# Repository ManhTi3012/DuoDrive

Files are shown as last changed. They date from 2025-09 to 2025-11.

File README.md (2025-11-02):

# ⚠️ **WARNING: PROJECT UNDER DEVELOPMENT, CHANGES WILL BE MADE**
<p align="center" style="display: flex; gap: 10px;">
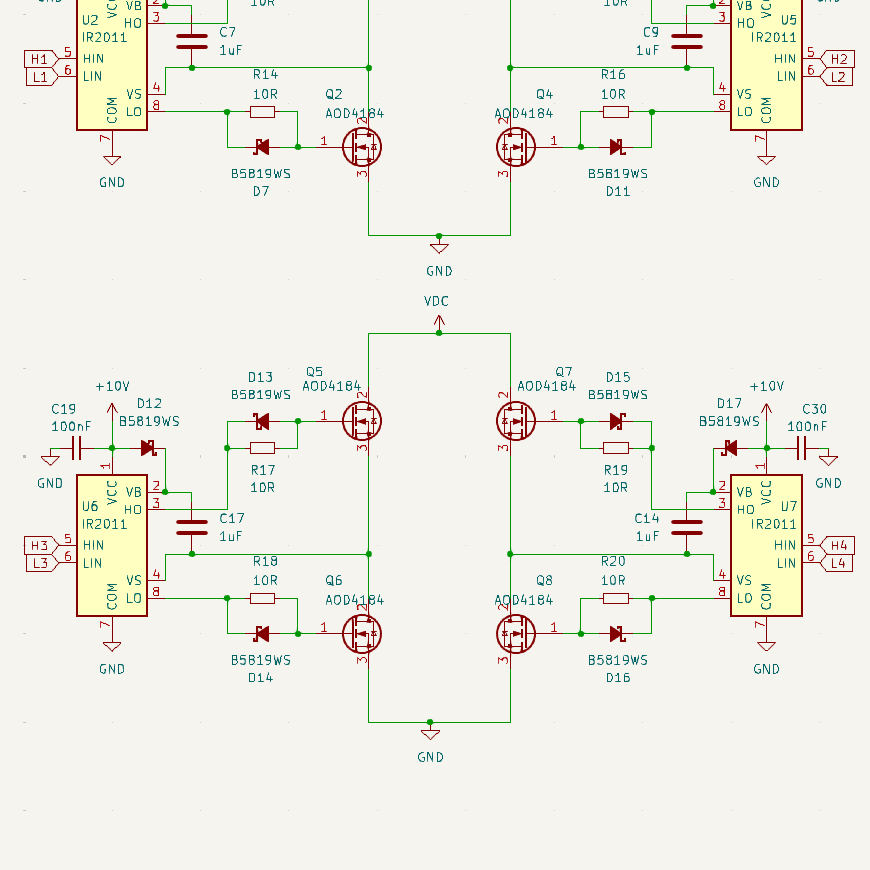
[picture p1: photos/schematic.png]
  
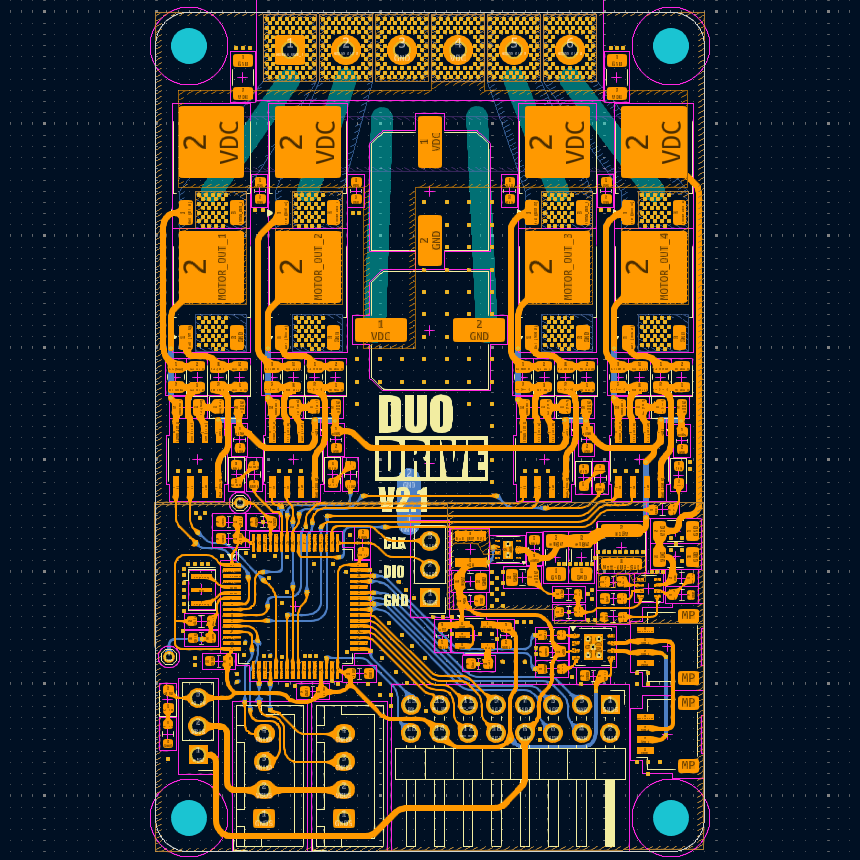
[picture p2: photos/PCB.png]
  
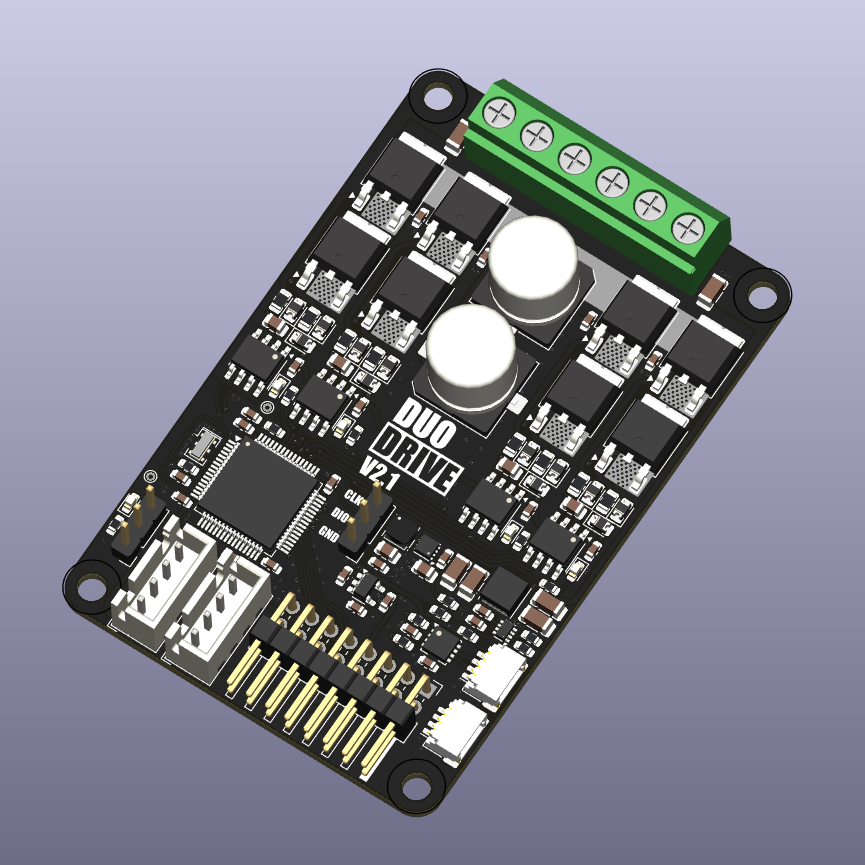
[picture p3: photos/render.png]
  
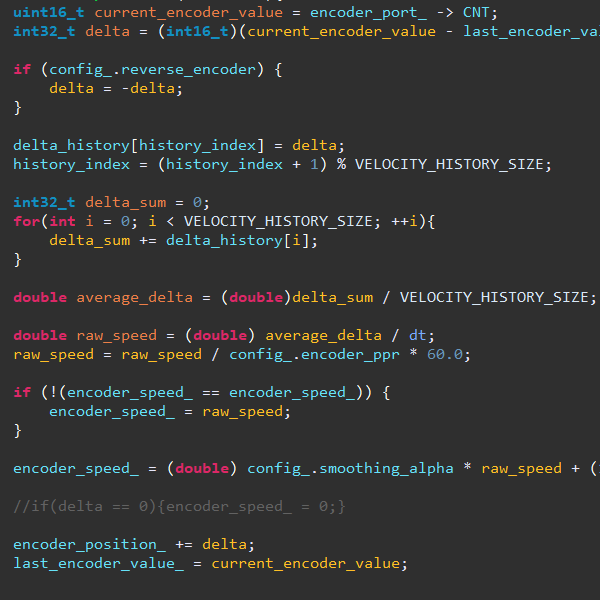
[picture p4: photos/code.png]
  
</p>

# DuoDrive
DuoDrive is a closed-loop brushed motor driver design to offer simple and affordable open-source hardware and software:
* Running internal PID loop for driving up to 2 brushed motor.
* Increment-type and absolute-type encoder (not yet).
* UART interface and CAN Bus (no firmware support yet).
* Velocity and position control.

You can also use SimpleFOC library to control a single BLDC motor.

<!---  An autonomous robot using DuoDrive's velocity control can still run straight without line or gyro correction.
  ![hi](https://github.com/ManhTi3012/DuoDrive/blob/main/photos/robot.gif) --->

For configuring the driver, checkout the [Web Tool](https://manhti3012.github.io/DuoDriveConfigTool/)

# Hardware
DuoDrive is designed to handle high current within a small footprint:
* Voltage input: 12-24v, 30V absolute maximum
* Maximum continuous current: 25A
* Power traces are exposed for high current handling, beware of shorts
* Dimensions: 49mm x 75mm

Step file can be found in "3D" folder.
# Firmware
The firmware is expected to be stable for now, but further testing still needed for stability-related bugs.
Please open a new issues if you encounter any problem.
For detailed explanation and methods, check Wiki page.

# Documentation
For more detail, check the [WIKI Page](https://github.com/ManhTi3012/DuoDrive/wiki)

# Liability
* The software and hardware are still in development and may contain bugs, errors, or incomplete features.
* Users are encouraged to use this software and hardware responsibly and at their own risk.

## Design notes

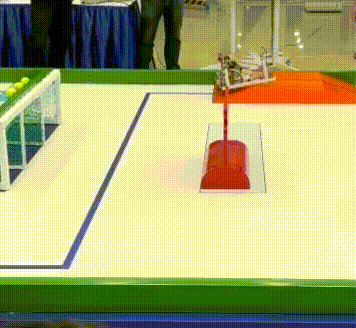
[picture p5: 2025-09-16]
photos/robot.gif

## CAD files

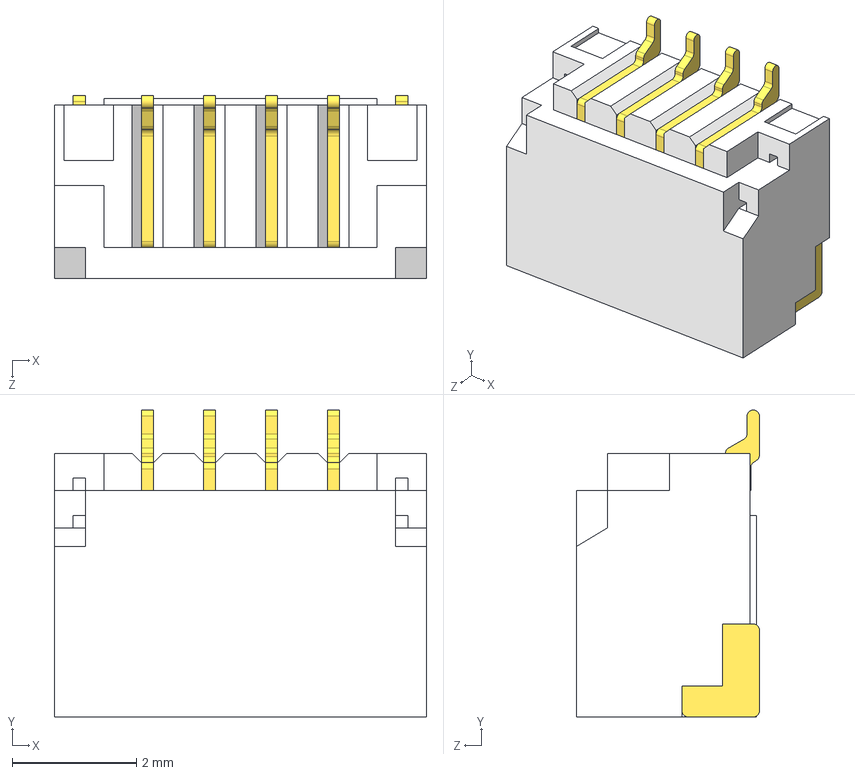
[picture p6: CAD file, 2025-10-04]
3D/SH1.0 Straight 4P.STEP
6.00 x 4.95 x 2.95 mm

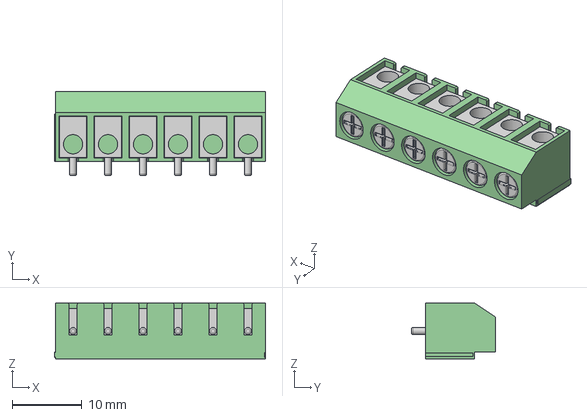
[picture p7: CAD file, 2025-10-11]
3D/Screw Terminal Block 5mm 6-way.step
30.1 x 12.0 x 8.00 mm

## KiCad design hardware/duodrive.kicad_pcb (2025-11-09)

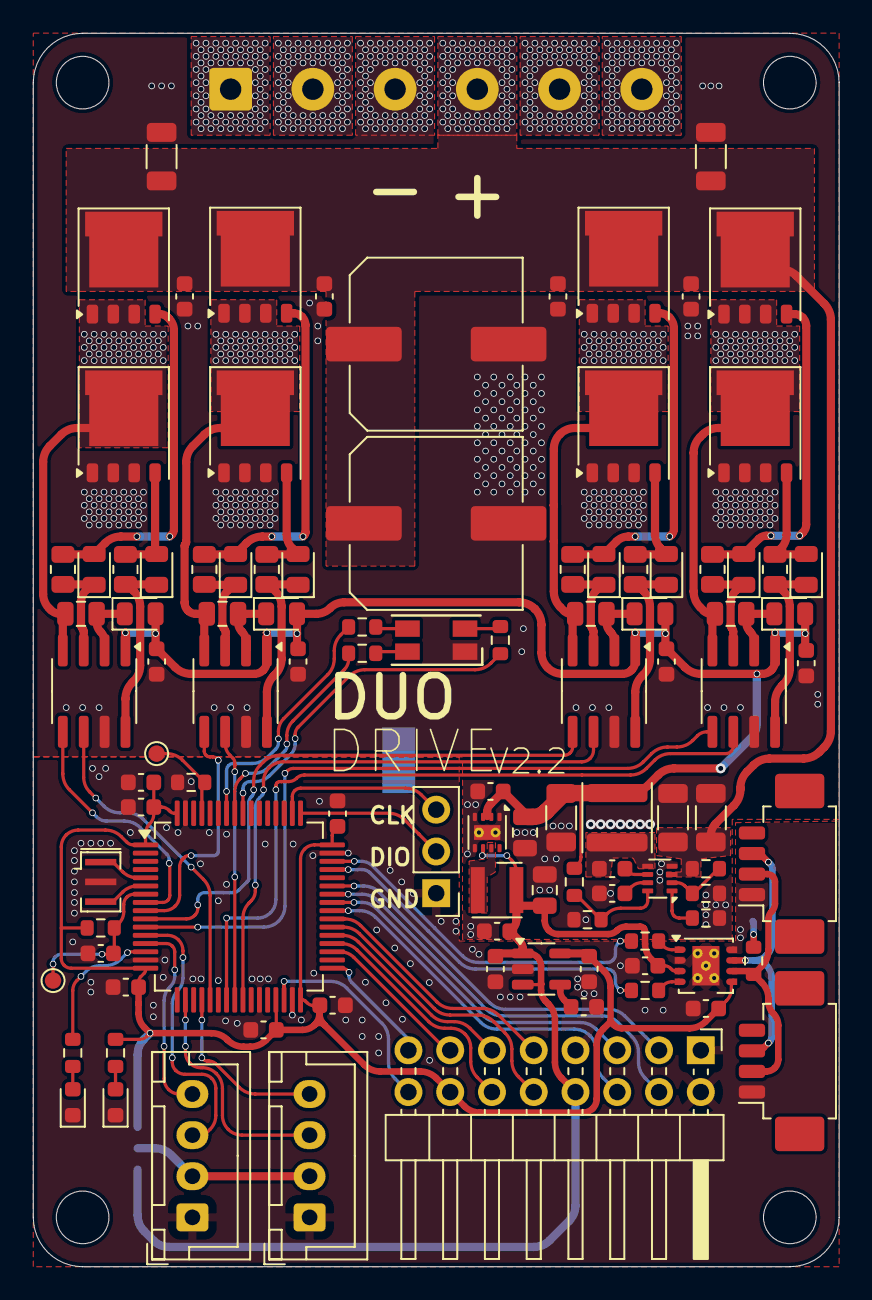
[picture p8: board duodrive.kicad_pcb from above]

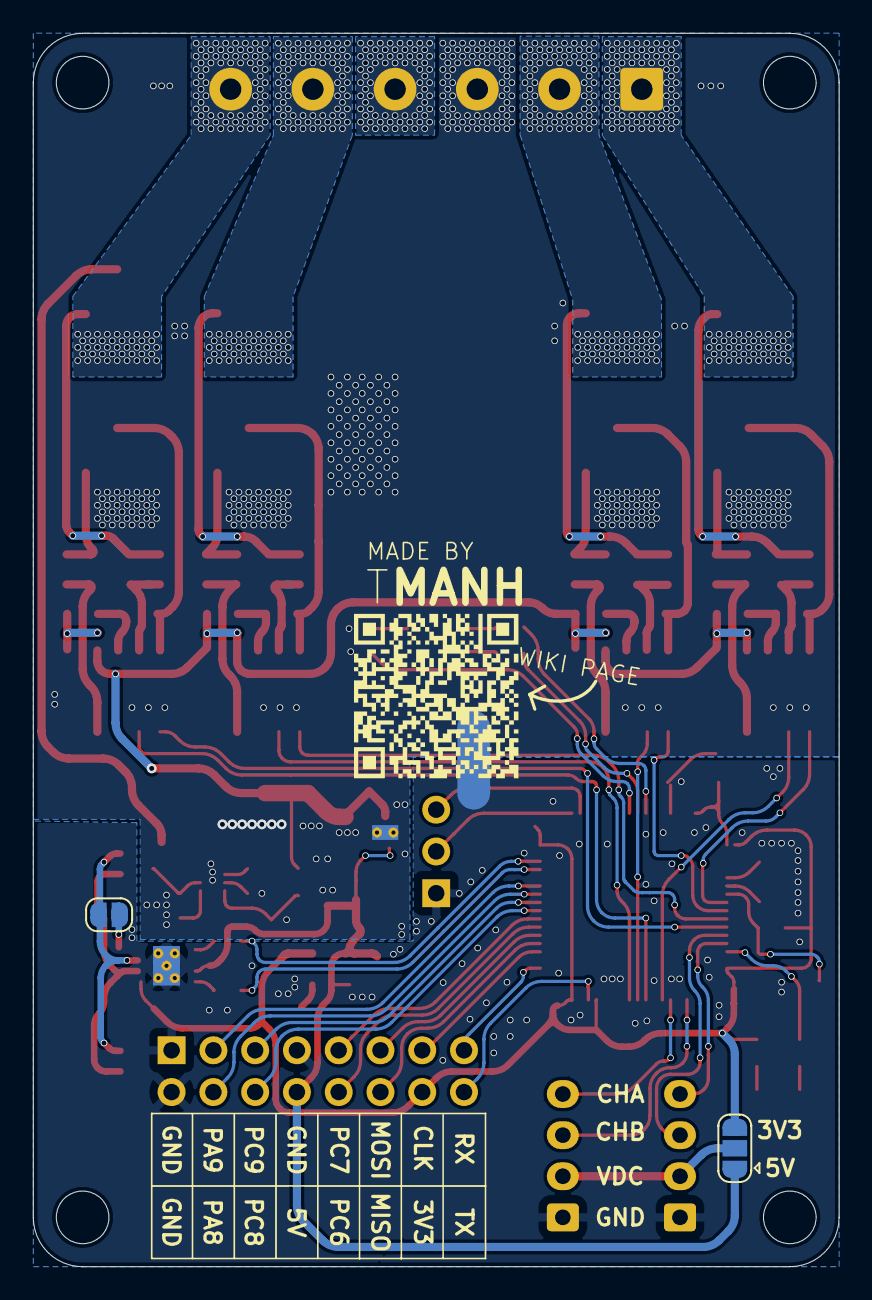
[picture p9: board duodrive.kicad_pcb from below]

Board: 2 copper layers, 49.0 x 75.0 mm, 111 parts (3 on the bottom side), 84 nets.

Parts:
C1, C3: 470uF; C_Elec_10x10.2
C2, C4, C5, C6, C8, C11, C13, C15, C16, C19, C21, C22, C25, C30, C36, C41, C42: 100nF; C_0603_1608Metric
C7, C9, C14, C17: 1uF; C_0805_2012Metric
C10, C12: 10uF; C_0603_1608Metric
C18, C20, C27: 10uF; C_1206_3216Metric
C23, C24: 22uF; C_1206_3216Metric
C26: 470pF; C_0603_1608Metric
C29, C31: 22uF; C_0805_2012Metric
C32, C33, C34, C35: 1uF; C_0603_1608Metric
D1, D20: LED_Small; LED_0603_1608Metric
D4: LED_KRGB; LED_RGB_1210
D6, D7, D8, D9, D10, D11, D12, D13, D14, D15, D16, D17: B5819WS; D_0805_2012Metric
H1, H2, H3, H4: MountingHole_Pad; MountingHole_3.2mm_M3
J2: Conn_02x08_Odd_Even; PinHeader_2x08_P2.54mm_Horizontal
J3: SWD; PinHeader_1x03_P2.54mm_Vertical
J4: CAN_IN; Molex_PicoBlade_53261-0471_1x04-1MP_P1.25mm_Horizontal
J5: CAN_OUT; Molex_PicoBlade_53261-0471_1x04-1MP_P1.25mm_Horizontal
J6: POWER; TerminalBlock_MetzConnect_Type094_RT03506HBLU_1x06_P5.00mm_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
J7: ENCODER1; JST_XH_B4B-XH-A_1x04_P2.50mm_Vertical
J8: ENCODER2; JST_XH_B4B-XH-A_1x04_P2.50mm_Vertical
JP1: Jumper_2_Open; SolderJumper-2_P1.3mm_Open_RoundedPad1.0x1.5mm
JP2: Jumper_3_Open; SolderJumper-3_P1.3mm_Open_RoundedPad1.0x1.5mm
L1: 12uH; L_APV_ANR4020
L2: 2.2uH; L_Wurth_WE-LQSH-3012
NT1: NetTie_2; NetTie-2_SMD_Pad2.0mm
Q1, Q2, Q3, Q4, Q5, Q7: DON50N04; PQFN-8-EP_6x5mm_P1.27mm_Generic
Q6, Q8: NMOS-8PINS; PQFN-8-EP_6x5mm_P1.27mm_Generic
R1, R3, R8, R9, R10, R11: 1K; R_0603_1608Metric
R2, R5, R6: 10K; R_0603_1608Metric
R4: 115K; R_0603_1608Metric
R7: 470K; R_0603_1608Metric
R12: 56K; R_0603_1608Metric
R13, R14, R15, R16, R17, R18, R19, R20: 10R; R_0805_2012Metric
R21, R22: 47R; R_0603_1608Metric
R23: 120R; R_0603_1608Metric
TP1, TP2: TestPoint; TestPoint_Pad_D1.0mm
U1: TCAN1044V; Texas_S-PVSON-N8_ThermalVias
U2, U5, U6, U7: UCC27211; SOIC-8_3.9x4.9mm_P1.27mm
U3: TPS62173DSG; WSON-8-1EP_2x2mm_P0.5mm_EP0.9x1.6mm_ThermalVias
U4: STM32G431RBTx; LQFP-64_10x10mm_P0.5mm
U8: TPS62933; SOT-583-8
U10: MIC5219-3.3YM5; SOT-23-5
Y1: Resonator; Resonator_SMD_Murata_CSTxExxV-3Pin_3.0x1.1mm

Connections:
+3.3V: C2.1, C4.1, C8.1, C11.1, C12.1, C21.1, C22.1, C36.1, J2.14, JP2.3 (B), R5.2, R8.1, U1.5 (VIO), U4.1 (VBAT), U4.16 (VDD), U4.29 (VDDA), U4.32 (VDD), U4.48 (VDD), U4.64 (VDD), U10.5 (OUT)
+5V: C10.1, C13.1, C31.1, C42.1, J2.8, JP2.1 (A), L2.2, U1.3 (VCC), U3.6 (VOS), U10.1 (IN), U10.3 (EN)
+10V: C15.1, C16.1, C19.1, C20.2, C29.1, C30.1, C41.1, D8.2 (A), D9.2 (A), D12.2 (A), D17.2 (A), L1.2, R4.2, U2.1 (VCC), U3.2 (VIN), U3.3 (EN), U5.1 (VCC), U6.1 (VCC), U7.1 (VCC)
BOOT: R2.2, TP1.1, U4.61 (PB8)
CANRX: R21.1, U4.45 (PA11)
CANTX: R22.1, U4.46 (PA12)
CAN_H: J4.3, J5.3, JP1.1 (A), U1.7 (CANH)
CAN_L: J4.2, J5.2, R23.2, U1.6 (CANL)
GND: C1.2, C3.2, C15.2, C16.2, C18.1, C19.2, C20.1, C23.1, C24.1, C25.1, C27.1, C29.2, C30.2, C31.2, C32.2, C33.2, C34.2, C35.2, C41.2, C42.2, D4.1 (K), J6.3, NT1.2, Q2.1 (S), Q2.2 (S), Q2.3 (S), Q4.1 (S), Q4.2 (S), Q4.3 (S), Q6.1 (S), Q6.2 (S), Q6.3 (S), Q8.1 (S), Q8.2 (S), Q8.3 (S), R6.1, R11.1, R12.2, U2.7 (COM), U3.1 (PGND), U3.4 (AGND), U3.5 (FB), U3.9 (PAD), U5.7 (COM), U6.7 (COM), U7.7 (COM), U8.4 (GND)
GNDS: C2.2, C4.2, C5.1, C8.2, C10.2, C11.2, C12.2, C13.2, C21.2, C22.2, C26.2, C36.2, D1.1 (K), D20.1 (K), J2.1, J2.2, J2.7, J3.1, J4.1, J5.1, J7.1, J8.1, NT1.1, R2.1, U1.2 (GND), U1.8 (STB), U1.9 (THERMAL), U4.15 (VSS), U4.27 (VSSA), U4.31 (VSS), U4.47 (VSS), U4.63 (VSS), U10.2 (GND), Y1.2
H1: U2.5 (HIN), U4.8 (PC0)
H2: U4.9 (PC1), U5.5 (HIN)
H3: U4.10 (PC2), U6.5 (HIN)
H4: U4.11 (PC3), U7.5 (HIN)
L1: U2.6 (LIN), U4.21 (PA7)
L2: U4.24 (PB0), U5.6 (LIN)
L3: U4.25 (PB1), U6.6 (LIN)
L4: U4.23 (PC5), U7.6 (LIN)
LED1: R1.1, U4.14 (PA2)
LED2: R9.1, U4.58 (PB5)
LED3: R10.1, U4.57 (PB4)
LED4: R3.1, U4.56 (PB3)
MOTOR_OUT_1: C7.2, J6.1, Q1.1 (S), Q1.2 (S), Q1.3 (S), Q2.5 (D), U2.4 (VS)
MOTOR_OUT_2: C9.2, J6.2, Q3.1 (S), Q3.2 (S), Q3.3 (S), Q4.5 (D), U5.4 (VS)
MOTOR_OUT_3: C17.2, J6.5, Q5.1 (S), Q5.2 (S), Q5.3 (S), Q6.5 (D), U6.4 (VS)
MOTOR_OUT_4: C14.2, J6.6, Q7.1 (S), Q7.2 (S), Q7.3 (S), Q8.5 (D), U7.4 (VS)
unnamed: D1.2 (A), R1.2
unnamed: D4.4 (BA), R10.2
unnamed: D4.3 (GA), R9.2
unnamed: D4.2 (RA), R3.2
unnamed: D6.2 (A), Q1.4 (G), R13.1
unnamed: D6.1 (K), R13.2, U2.3 (HO)
unnamed: D7.2 (A), Q2.4 (G), R14.1
unnamed: D7.1 (K), R14.2, U2.8 (LO)
unnamed: C7.1, D8.1 (K), U2.2 (VB)
unnamed: C9.1, D9.1 (K), U5.2 (VB)
unnamed: D10.2 (A), Q3.4 (G), R15.1
unnamed: D10.1 (K), R15.2, U5.3 (HO)
unnamed: D11.2 (A), Q4.4 (G), R16.1
unnamed: D11.1 (K), R16.2, U5.8 (LO)
unnamed: C17.1, D12.1 (K), U6.2 (VB)
unnamed: D13.2 (A), Q5.4 (G), R17.1
unnamed: D13.1 (K), R17.2, U6.3 (HO)
unnamed: D14.2 (A), Q6.4 (G), R18.1
unnamed: D14.1 (K), R18.2, U6.8 (LO)
unnamed: D15.2 (A), Q7.4 (G), R19.1
unnamed: D15.1 (K), R19.2, U7.3 (HO)
unnamed: D16.2 (A), Q8.4 (G), R20.1
unnamed: D16.1 (K), R20.2, U7.8 (LO)
unnamed: C14.1, D17.1 (K), U7.2 (VB)
unnamed: D20.2 (A), R8.2
unnamed: JP1.2 (B), R23.1
unnamed: R21.2, U1.4 (RXD)
unnamed: R22.2, U1.1 (TXD)
unnamed: L2.1, U3.7 (SW)
unnamed: U4.5 (PF0), Y1.1
unnamed: U4.6 (PF1), Y1.3
unnamed: C6.2, U8.6 (BST)
unnamed: R7.1, R12.1, U8.2 (EN)
unnamed: R4.1, R6.2, U8.8 (FB)
unnamed: R11.2, U8.1 (RT)
unnamed: C25.2, U8.7 (SS)
unnamed: C6.1, L1.1, U8.5 (SW)
unnamed: C26.1, U10.4 (BP)
PA8: J2.4, U4.42 (PA8)
PA9: J2.3, U4.43 (PA9)
PC6: J2.10, U4.38 (PC6)
PC7: J2.9, U4.39 (PC7)
PC8: J2.6, U4.40 (PC8)
PC9: J2.5, U4.41 (PC9)
PWM1A: J7.3, U4.12 (PA0)
PWM1B: J7.4, U4.13 (PA1)
PWM2A: J8.3, U4.18 (PA4)
PWM2B: J8.4, U4.20 (PA6)
RX: J2.15, U4.33 (PB11)
Reset: C5.2, R5.1, TP2.1, U4.7 (PG10)
SPI_CLK: J2.13, U4.35 (PB13)
SPI_MISO: J2.12, U4.36 (PB14)
SPI_MOSI: J2.11, U4.37 (PB15)
SWCLK: J3.3, U4.50 (PA14)
SWDIO: J3.2, U4.49 (PA13)
TX: J2.16, U4.30 (PB10)
VBUS: J7.2, J8.2, JP2.2 (C)
VDC: C1.1, C3.1, C18.2, C23.2, C24.2, C27.2, C32.1, C33.1, C34.1, C35.1, J6.4, Q1.5 (D), Q3.5 (D), Q5.5 (D), Q7.5 (D), R7.2, U8.3 (VIN)

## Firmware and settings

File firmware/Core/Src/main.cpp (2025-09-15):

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
/* Includes ------------------------------------------------------------------*/
#include "main.h"

/* USER CODE BEGIN Includes */
#include "led_control.h"
#include "motor_control.h"
#include "uart_parser.h"
#include "flash_store_data.h"
#include "constants.h"
#include <string.h>
/* USER CODE END Includes */

CRC_HandleTypeDef hcrc;

FDCAN_HandleTypeDef hfdcan1;

TIM_HandleTypeDef htim1;
TIM_HandleTypeDef htim2;
TIM_HandleTypeDef htim3;
TIM_HandleTypeDef htim6;
TIM_HandleTypeDef htim16;
TIM_HandleTypeDef htim17;

UART_HandleTypeDef huart3;
DMA_HandleTypeDef hdma_usart3_rx;

/* USER CODE BEGIN PV */
// Config
Motor motor1;
Motor motor2;
// UART command
//uint8_t RxData[10];
//uint8_t RxCommand[256];
//uint8_t RxIndex;
//volatile bool RxReceiving = true;
//char CommandType = '#';  // Default

#define RX_BUFFER_SIZE 256

uint8_t DMA_RX_Buffer[RX_BUFFER_SIZE]; // DMA circular buffer
uint8_t Parse_Buffer[RX_BUFFER_SIZE];  // Final buffer to parse

volatile uint16_t old_pos = 0;
volatile uint8_t data_ready = 0;
volatile uint8_t uart_processing = 0;

/* USER CODE END PV */

void SystemClock_Config(void);
static void MX_GPIO_Init(void);
static void MX_DMA_Init(void);
static void MX_FDCAN1_Init(void);
static void MX_TIM1_Init(void);
static void MX_TIM2_Init(void);
static void MX_TIM3_Init(void);
static void MX_USART3_UART_Init(void);
static void MX_TIM16_Init(void);
static void MX_TIM17_Init(void);
static void MX_CRC_Init(void);
static void MX_TIM6_Init(void);
/* USER CODE BEGIN PFP */
extern "C" void BufferProcessing(void);
/* USER CODE END PFP */

/**
  * @brief  The application entry point.
  * @retval int
  */
int main(void)
{

  /* MCU Configuration--------------------------------------------------------*/

  /* Reset of all peripherals, Initializes the Flash interface and the Systick. */
  HAL_Init();

  /* Configure the system clock */
  SystemClock_Config();

  /* Initialize all configured peripherals */
  MX_GPIO_Init();
  MX_DMA_Init();
  MX_FDCAN1_Init();
  MX_TIM1_Init();
  MX_TIM2_Init();
  MX_TIM3_Init();
  MX_USART3_UART_Init();
  MX_TIM16_Init();
  MX_TIM17_Init();
  MX_CRC_Init();
  MX_TIM6_Init();
  /* USER CODE BEGIN 2 */
  HAL_TIM_PWM_Start(&htim1, TIM_CHANNEL_1);
  HAL_TIMEx_PWMN_Start(&htim1, TIM_CHANNEL_1);

  HAL_TIM_PWM_Start(&htim1, TIM_CHANNEL_2);
  HAL_TIMEx_PWMN_Start(&htim1, TIM_CHANNEL_2);

  HAL_TIM_PWM_Start(&htim1, TIM_CHANNEL_3);
  HAL_TIMEx_PWMN_Start(&htim1, TIM_CHANNEL_3);

  HAL_TIM_PWM_Start(&htim1, TIM_CHANNEL_4);
  HAL_TIMEx_PWMN_Start(&htim1, TIM_CHANNEL_4);

  HAL_TIM_Encoder_Start(&htim2, TIM_CHANNEL_ALL);
  HAL_TIM_Encoder_Start(&htim3, TIM_CHANNEL_ALL);

  HAL_TIM_Base_Start_IT(&htim16);
  HAL_TIM_Base_Start_IT(&htim17);
  HAL_TIM_Base_Start_IT(&htim6);

  load_config_from_flash();

  motor1.Init(TIM1, 1, TIM1, 2, TIM17);
  motor1.InitEncoder(TIM2);
  motor1.LoadConfig(current_config.motor1);

  motor2.Init(TIM1, 3, TIM1, 4, TIM16);
  motor2.InitEncoder(TIM3);
  motor2.LoadConfig(current_config.motor2);


  // Start UART DMA
//  HAL_UART_Receive_DMA(&huart3, RxData, 1);
  HAL_UART_Receive_DMA(&huart3, DMA_RX_Buffer, RX_BUFFER_SIZE);
  __HAL_UART_ENABLE_IT(&huart3, UART_IT_ERR);  // enable all error interrupts

  /* USER CODE END 2 */

  /* Infinite loop */
  /* USER CODE BEGIN WHILE */
  while (1)
  {
    /* USER CODE END WHILE */

    /* USER CODE BEGIN 3 */
//	  if (data_ready) {
//	      data_ready = 0;
//
//	      char *start = strchr((char *)Parse_Buffer, '#');
//	      if (!start) start = strchr((char *)Parse_Buffer, '@');
//
//	      while (start) {
//	          char *end = strchr(start, '\n');
//	          if (!end) break;
//
//	          *end = '\0';
//
//	          if (start[0] == '#') parse(start + 1);
//	          else if (start[0] == '@') machineParse(start + 1);
//
//	          start = strchr(end + 1, '#');
//	          if (!start) start = strchr(end + 1, '@');
//	      }
//	  }
	  BufferProcessing();
  }
  /* USER CODE END 3 */
}

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
/* USER CODE BEGIN 4 */
//void BufferProcessing(){
//	if (!uart_processing) {
//	    uart_processing = 1;
//
//	    HAL_GPIO_TogglePin(GPIOB, GPIO_PIN_5);
//
//	    uint16_t pos = RX_BUFFER_SIZE - __HAL_DMA_GET_COUNTER(huart3.hdmarx);
//
//	    if (pos != old_pos) {
//	        uint16_t len;
//	        if (pos > old_pos) {
//	            len = pos - old_pos;
//	            memcpy(Parse_Buffer, &DMA_RX_Buffer[old_pos], len);
//	        } else {
//	            len = RX_BUFFER_SIZE - old_pos;
//	            memcpy(Parse_Buffer, &DMA_RX_Buffer[old_pos], len);
//	            memcpy(Parse_Buffer + len, DMA_RX_Buffer, pos);
//	            len += pos;
//	        }
//
//	        Parse_Buffer[len] = '\0';
//	        old_pos = pos;
//	        data_ready = 1;
//	    }
//
//	    uart_processing = 0;
//	}
//}

void BufferProcessing() {
	HAL_GPIO_TogglePin(GPIOB, GPIO_PIN_6);
    static uint16_t parse_len = 0; // leftover bytes in Parse_Buffer

    uint16_t pos = RX_BUFFER_SIZE - __HAL_DMA_GET_COUNTER(huart3.hdmarx); // current write pos

    if (pos == old_pos) return; // nothing new

    uint16_t len = 0;

    if (pos > old_pos) {
        len = pos - old_pos;
        // guard overflow
        if (parse_len + len >= RX_BUFFER_SIZE) {
            // overflow: discard buffer to recover
            parse_len = 0;
            old_pos = pos;
            return;
        }
        memcpy(&Parse_Buffer[parse_len], &DMA_RX_Buffer[old_pos], len);
    } else { // wrapped around
        len = RX_BUFFER_SIZE - old_pos;
        if (parse_len + len >= RX_BUFFER_SIZE) { parse_len = 0; old_pos = pos; return; }
        memcpy(&Parse_Buffer[parse_len], &DMA_RX_Buffer[old_pos], len);

        if (pos > 0) {
            if (parse_len + len + pos >= RX_BUFFER_SIZE) { parse_len = 0; old_pos = pos; return; }
            memcpy(&Parse_Buffer[parse_len + len], DMA_RX_Buffer, pos);
            len += pos;
        }
    }

    parse_len += len;
    old_pos = pos;

    // parse complete lines
    uint16_t read_idx = 0;
    for (uint16_t i = 0; i < parse_len; i++) {
        if (Parse_Buffer[i] == '\n') {
            // determine line boundaries [read_idx ... i]
            uint16_t line_start = read_idx;
            uint16_t line_end = i; // '\n' at i

            // remove optional trailing '\r'
            if (line_end > line_start && Parse_Buffer[line_end - 1] == '\r') {
                Parse_Buffer[line_end - 1] = '\0';
            } else {
                Parse_Buffer[line_end] = '\0';
            }

            // find first marker in the line: '#' or '@'
            char *marker = NULL;
            for (uint16_t k = line_start; k < line_end; k++) {
                if (Parse_Buffer[k] == '#' || Parse_Buffer[k] == '@') {
                    marker = (char *)&Parse_Buffer[k];
                    break;
                }
            }

            if (marker) {
                if (marker[0] == '#') {
                    parse(marker + 1);
                } else {
                    machineParse(marker + 1);
                }
            } else {
                // no marker found — ignore the line
            }

            read_idx = i + 1; // move past this line
        }
    }

    // move leftover partial data to start of buffer
    if (read_idx < parse_len) {
        uint16_t leftover = parse_len - read_idx;
        memmove(Parse_Buffer, &Parse_Buffer[read_idx], leftover);
        parse_len = leftover;
    } else {
        parse_len = 0;
    }
}


void HAL_UART_ErrorCallback(UART_HandleTypeDef *huart) {
    if (huart == &huart3) {
        // Clear all error flags just in case
        __HAL_UART_CLEAR_FEFLAG(huart);
        __HAL_UART_CLEAR_NEFLAG(huart);
        __HAL_UART_CLEAR_OREFLAG(huart);

        // Restart DMA to recover
        HAL_UART_AbortReceive(huart);
        HAL_UART_Receive_DMA(huart, DMA_RX_Buffer, RX_BUFFER_SIZE);
    }
}

void HAL_TIM_PeriodElapsedCallback(TIM_HandleTypeDef* htim)
{
	if(htim->Instance == TIM17){
		static uint16_t vel_counter = 0;
		static uint16_t pos_counter = 0;

		double dt = (double)(motor1.GetARR() + 1) / 10000;
		uint16_t pos_loop_scale = motor1.GetPScale();
		uint16_t vel_loop_scale = motor1.GetVScale();
		// Velocity loop
		if (vel_loop_scale > 0) {
		    if (vel_counter > 0) {
		        vel_counter--;
		    }
		    if (vel_counter == 0) {
		        motor1.UpdateData(dt);
		        motor1.VelocityLoop(dt);
		        vel_counter = vel_loop_scale;
		    }
		}
		// Position loop
		if (pos_loop_scale > 0) {
		    if (pos_counter > 0) {
		        pos_counter--;
		    }
		    if (pos_counter == 0) {
		        motor1.PositionLoop(dt);
		        pos_counter = pos_loop_scale;
		    }
		}

	}
	if(htim->Instance == TIM16){
		static uint16_t vel_counter = 0;
		static uint16_t pos_counter = 0;

		double dt = (double)(motor2.GetARR() + 1) / 10000;
		uint16_t pos_loop_scale = motor2.GetPScale();
		uint16_t vel_loop_scale = motor2.GetVScale();
		// Velocity loop
		if (vel_loop_scale > 0) {
		    if (vel_counter > 0) {
		        vel_counter--;
		    }

		    if (vel_counter == 0) {
		        motor2.UpdateData(dt);
		        motor2.VelocityLoop(dt);
		        vel_counter = vel_loop_scale;
		    }
		}
		// Position loop
		if (pos_loop_scale > 0) {
		    if (pos_counter > 0) {
		        pos_counter--;
		    }

		    if (pos_counter == 0) {
		        motor2.PositionLoop(dt);
		        pos_counter = pos_loop_scale;
		    }
		}
	}
//    if (htim->Instance == TIM6) {
//    	BufferProcessing();
//    }
}
/* USER CODE END 4 */
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


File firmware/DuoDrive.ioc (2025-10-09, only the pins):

Mcu.UserName=STM32G431RBTx
PA0.Signal=S_TIM2_CH1
PA1.Signal=S_TIM2_CH2
PA11.Signal=FDCAN1_RX
PA12.Signal=FDCAN1_TX
PA13.Signal=SYS_JTMS-SWDIO
PA14.Signal=SYS_JTCK-SWCLK
PA4.Signal=S_TIM3_CH2
PA6.Signal=S_TIM3_CH1
PA7.Signal=TIM1_CH1N
PB0.Signal=TIM1_CH2N
PB1.Signal=TIM1_CH3N
PB10.Signal=USART3_TX
PB11.Signal=USART3_RX
PB13.Signal=SPI2_SCK
PB14.Signal=SPI2_MISO
PB15.Signal=SPI2_MOSI
PB3.Signal=GPIO_Output
PB4.Signal=GPIO_Output
PB5.Signal=GPIO_Output
PB6.Signal=GPIO_Output
PB8-BOOT0.Signal=GPIO_Input
PC0.Signal=S_TIM1_CH1
PC1.Signal=S_TIM1_CH2
PC2.Signal=S_TIM1_CH3
PC3.Signal=S_TIM1_CH4
PC5.Signal=TIM1_CH4N
PC8.Signal=I2C3_SCL
PC9.Signal=I2C3_SDA
PF0-OSC_IN.Signal=RCC_OSC_IN
PF1-OSC_OUT.Signal=RCC_OSC_OUT

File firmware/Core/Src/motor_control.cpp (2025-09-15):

/*
 * motor_control.c
 *
 *  Created on: Apr 29, 2025
 *      Author: Ti Manh
 */

#include "motor_control.h"
#include <stdlib.h>
#include <stdio.h>


bool Motor::Init(TIM_TypeDef *timer_left, uint8_t channel_left,TIM_TypeDef *timer_right, uint8_t channel_right, TIM_TypeDef* pid_timer){
	if(channel_right > 4 || channel_left > 4){
		return false;
	}
	L_TIM = timer_left;
	L_CHN = channel_left;
	R_TIM = timer_right;
	R_CHN = channel_right;

	pid_timer_ = pid_timer;

	LoadConfig(default_motor);
	return true;
}

void Motor::InitEncoder(TIM_TypeDef *timer_encoder){
	has_encoder_ = true;
	encoder_port_ = timer_encoder;
}

void Motor::LoadConfig(MotorConfig config){
	this->config_ = config;

    pid.position.setGains(config_.position_kp, config_.position_ki, config_.position_kd);
    pid.position.setOutputLimits(-config_.max_velocity, config_.max_velocity);

    pid.velocity.setGains(config_.velocity_kp, config_.velocity_ki, config_.velocity_kd);
    pid.velocity.setOutputLimits(-MAX_DUTY, MAX_DUTY);
}

MotorConfig Motor::GetConfig() {
    return config_;
}

void Motor::PositionMode(double target){
	if(!has_encoder_){return;}
	else{
		current_mode_ = POSITION;
		target_position_ = target;

	}
}
void Motor::VelocityMode(double target){
	if(!has_encoder_){return;}
	else{
		current_mode_ = VELOCITY;
		target_velocity_ = target;
	}
}

void Motor::OpenLoopMode(int16_t pwm){
	current_mode_ = OPEN_LOOP;
	target_pwm_ = pwm;
}

void Motor::ResetPos(){
	encoder_port_->CNT = 0;
	last_encoder_value_ = 0;
	encoder_position_ = 0;
}

void Motor::ResetPos(int64_t new_position){
	encoder_port_->CNT = 0;
	last_encoder_value_ = 0;
	encoder_position_ = new_position;
}

void Motor::SetMaxVel(double max_vel){
	config_.max_velocity = max_vel;
}

void Motor::SetAlpha(double alpha){
	config_.smoothing_alpha = alpha;
}

void Motor::ReverseEncoder(bool reverse){
	config_.reverse_encoder = reverse;
}

void Motor::SetARR(uint16_t arr){
	config_.pid_arr = arr;
	pid_timer_->ARR = arr;
}

void Motor::SetVScale(uint16_t vscale){
	config_.vel_scale = vscale;
}
void Motor::SetPScale(uint16_t pscale){
	config_.pos_scale = pscale;
}

void Motor::SetPPR(uint32_t ppr){
	config_.encoder_ppr = ppr;
}
void Motor::SetRampSpeed(uint16_t ramp_speed){
	config_.ramp_speed = ramp_speed;
}

void Motor::SetGainP(double set_Kp, double set_Ki, double set_Kd){
	pid.position.setGains(set_Kp, set_Ki, set_Kd);
}
void Motor::SetGainV(double set_Kp, double set_Ki, double set_Kd){
	pid.velocity.setGains(set_Kp, set_Ki, set_Kd);
}

double Motor::GetMaxVel(){
	return config_.max_velocity;
}

double Motor::GetAlpha(){
	return config_.smoothing_alpha;
}

bool Motor::IsEncoderReversed(){
	return config_.reverse_encoder;
}



uint16_t Motor::GetARR(){
	return config_.pid_arr;
}
uint16_t Motor::GetPScale(){
	return config_.pos_scale;
}
uint16_t Motor::GetVScale(){
	return config_.vel_scale;
}
uint32_t Motor::GetPPR(){
	return config_.encoder_ppr;
}

uint16_t Motor::GetRampSpeed(){
	return config_.ramp_speed;
}

void Motor::GetGainP(double &p, double &i, double &d){
	pid.position.getGains(p, i, d);
}
void Motor::GetGainV(double &p, double &i, double &d){
	pid.velocity.getGains(p, i, d);
}

int64_t Motor::GetPosition(){
	if(has_encoder_){
		return encoder_position_;
	}
	else{
		return 0;
	}
}

int16_t Motor::GetPwm(){
	return current_pwm_;
}

double Motor::GetRPM(){
	if(has_encoder_){
		return encoder_speed_;
	}
	else{
		return 0;
	}
}

void Motor::Update(double dt){
	UpdateData(dt);
	switch(current_mode_){
		case OPEN_LOOP:
			RampPwm(dt);
			break;
		case POSITION:
			target_velocity_ = pid.position.calculate(target_position_, encoder_position_, dt);
			target_pwm_ = pid.velocity.calculate(target_velocity_, encoder_speed_, dt);
			RampPwm(dt);
			break;
		case VELOCITY:
			target_pwm_ = pid.velocity.calculate(target_velocity_, encoder_speed_, dt);
			RampPwm(dt);
			break;
	}
}

void Motor::PositionLoop(double dt){
	if(current_mode_ == POSITION){
		target_velocity_ = pid.position.calculate(target_pwm_, encoder_position_, dt);
	}
	else{
		return;
	}
}

void Motor::VelocityLoop(double dt){
	if(current_mode_ == OPEN_LOOP){
		RampPwm(dt);
	}
	else{
		target_pwm_ = pid.velocity.calculate(target_velocity_, encoder_speed_, dt);
		RampPwm(dt);
	}
}

void Motor::UpdateData(double dt){
	uint16_t current_encoder_value = encoder_port_ -> CNT;
	int32_t delta = (int16_t)(current_encoder_value - last_encoder_value_);

	if (config_.reverse_encoder) {
		delta = -delta;
	}

	delta_history[history_index] = delta;
	history_index = (history_index + 1) % VELOCITY_HISTORY_SIZE;

	int32_t delta_sum = 0;
	for(int i = 0; i < VELOCITY_HISTORY_SIZE; ++i){
	    delta_sum += delta_history[i];
	}

	double average_delta = (double)delta_sum / VELOCITY_HISTORY_SIZE;

	double raw_speed = (double) average_delta / dt;
	raw_speed = raw_speed / config_.encoder_ppr * 60.0;

	if (!(encoder_speed_ == encoder_speed_)) {
	    encoder_speed_ = raw_speed;
	}

	encoder_speed_ = (double) config_.smoothing_alpha * raw_speed + (1.0 - config_.smoothing_alpha) * encoder_speed_;

	//if(delta == 0){encoder_speed_ = 0;}

	encoder_position_ += delta;
	last_encoder_value_ = current_encoder_value;
}

void Motor::SetPwm(int16_t pwm){
	//clamp pwm
	if(pwm > MAX_DUTY){
		pwm = MAX_DUTY;
	}
	else if(pwm < -MAX_DUTY){
		pwm = -MAX_DUTY;
	}

	if(pwm >= 0){
		// set left side driver to GND
	    switch (L_CHN) {
	        case 1: L_TIM->CCR1 = 0; break;
	        case 2: L_TIM->CCR2 = 0; break;
	        case 3: L_TIM->CCR3 = 0; break;
	        case 4: L_TIM->CCR4 = 0; break;
	        default: break;
	    }
	    // set right side driver to pwm
	    switch (R_CHN) {
	        case 1: R_TIM->CCR1 = pwm; break;
	        case 2: R_TIM->CCR2 = pwm; break;
	        case 3: R_TIM->CCR3 = pwm; break;
	        case 4: R_TIM->CCR4 = pwm; break;
	        default: break;
	    }
	}
	else{
		// set left side driver to pwm
	    switch (L_CHN) {
	        case 1: L_TIM->CCR1 = -pwm; break;
	        case 2: L_TIM->CCR2 = -pwm; break;
	        case 3: L_TIM->CCR3 = -pwm; break;
	        case 4: L_TIM->CCR4 = -pwm; break;
	        default: break;
	    }
	    // set right side driver to GND
	    switch (R_CHN) {
	        case 1: R_TIM->CCR1 = 0; break;
	        case 2: R_TIM->CCR2 = 0; break;
	        case 3: R_TIM->CCR3 = 0; break;
	        case 4: R_TIM->CCR4 = 0; break;
	        default: break;
	    }
	}
}

void Motor::RampPwm(double dt){
	double delta = (double) config_.ramp_speed * dt;
	if(current_pwm_ < target_pwm_){
		if(current_pwm_ + delta > target_pwm_){current_pwm_ = target_pwm_;}
		else{current_pwm_ += delta;}
	}
	else if (current_pwm_ > target_pwm_){
		if(current_pwm_ - delta < target_pwm_){current_pwm_ = target_pwm_;}
		else{current_pwm_ -= delta;}
	}
	SetPwm(current_pwm_);
}

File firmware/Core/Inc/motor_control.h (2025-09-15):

/*
 * motor_control.h
 *
 *  Created on: Apr 29, 2025
 *      Author: Ti Manh
 */

#ifndef INC_MOTOR_CONTROL_H_
#define INC_MOTOR_CONTROL_H_

#include "stm32g4xx_hal.h"
#include "constants.h"
#include "PID.h"

class Motor {
public:
	bool Init(TIM_TypeDef *timer_left, uint8_t channel_left,TIM_TypeDef *timer_right, uint8_t channel_right, TIM_TypeDef* pid_timer);
	void InitEncoder(TIM_TypeDef *timer_encoder);
	void LoadConfig(MotorConfig config);
	MotorConfig GetConfig();

	void PositionMode(double target);
	void VelocityMode(double target);
	void OpenLoopMode(int16_t pwm);

	void ResetPos();
	void ResetPos(int64_t new_position);

	void SetMaxVel(double max_vel);
	void SetAlpha(double alpha);

	void ReverseEncoder(bool reverse);

	void SetARR(uint16_t arr);
	void SetVScale(uint16_t vscale);
	void SetPScale(uint16_t pscale);

	void SetPPR(uint32_t ppr);
	void SetRampSpeed(uint16_t ramp_speed);

	void SetGainP(double set_Kp, double set_Ki, double set_Kd);
	void SetGainV(double set_Kp, double set_Ki, double set_Kd);

	double GetMaxVel();
	double GetAlpha();

	bool IsEncoderReversed();

	uint16_t GetARR();
	uint16_t GetVScale();
	uint16_t GetPScale();

	uint32_t GetPPR();
	uint16_t GetRampSpeed();

	void GetGainP(double &p, double &i, double &d);
	void GetGainV(double &p, double &i, double &d);

	int64_t GetPosition();
	int16_t GetPwm();
	double GetRPM();

	void UpdateData(double dt);
	void PositionLoop(double dt);
	void VelocityLoop(double dt);


private:

	TIM_TypeDef *L_TIM;
	uint8_t L_CHN;
	TIM_TypeDef *R_TIM;
	uint8_t R_CHN;
	TIM_TypeDef* pid_timer_;
	void SetPwm(int16_t pwm);
	void RampPwm(double dt);

	void Update(double dt); //Unused

    struct {
        PID position;  // Outer loop (position → velocity)
        PID velocity;  // Inner loop (velocity → PWM)
    } pid;

	enum ControlMode {
	    POSITION,
	    VELOCITY,
		OPEN_LOOP
	} current_mode_ = OPEN_LOOP;

	MotorConfig config_;

	int16_t target_pwm_ = 0;
    double current_pwm_ = 0;

    double target_velocity_ = 0;

    double target_position_ = 0;

	bool has_encoder_ = false;
	double encoder_speed_ = 0.0;

	TIM_TypeDef *encoder_port_;
	volatile int64_t encoder_position_;
	volatile uint16_t last_encoder_value_ = 0;

	int16_t delta_history[VELOCITY_HISTORY_SIZE] = {};
	int history_index = 0;

};

#endif /* INC_MOTOR_CONTROL_H_ */

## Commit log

2025-07-15 update and clean up
    clean up the tree and update 100+ files
    [brushed_double_v3.kicad_pcb, brushed_double_v3.kicad_sch, duodrive.kicad_pcb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]
2025-07-16 more uart commands and functions
2025-07-18 fix uart command
2025-07-24 Update Command and parsing
    fix and update all parse command, prepare machine command for a more efficient communication than human version
    [DuoDrive.ioc, main.cpp, motor_control.cpp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]
2025-07-24 UART parser update
    Added machine communication and fix print function
    [main.cpp, motor_control.cpp, motor_control.h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]
2025-07-25 Hardware bug fix
    Fixed buck converter output bulk capacitor not connected to ground
    Added pull up resistor at buck EN pin instead of connect it to VCC
    [duodrive.kicad_pcb, duodrive.kicad_sch]
2025-08-01 Remake Motor Control
    Add more config-able parameter, new Timer Interrupt-Based PID Clock
2025-08-05 Minor bug fix and QOL feature
    Minor bug fix:
    - Changed layout of buck converter for bigger capacitor and added pull up resistor
    - Fixed buck output capacitor connected to wrong pin
    - Changed passive component value to match final product value
    QOL Feature:
    - Added QR code on the bottom silkscreen for wiki page
    - SWD connector changed from 2mm to 2.54mm for easier debug or update
    - Grouping and separation in schematic layout for better visual clarity
    [duodrive.kicad_pcb, duodrive.kicad_sch]
2025-08-07 Bug fixes and new feature
    - Fix UART not able to receive constant data stream
    - Fix velocity calculation that result in wrong result
    - Now config can be saved in internal flash
    - All config are now able to change through UART command
    - New async PID loop, can be set between 1Hz and 10kHz
    [DuoDrive.ioc, constant.cpp, flash_store_data.cpp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]
2025-09-15 QOL Fix
    - Encoder PPR overflow fix
    - Changed uart parser method to DMA circular buffer from single char processing.
    [DuoDrive.ioc, constant.cpp, main.cpp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]
2025-10-04 NEW Version
    [SH1.0 Straight 4P.STEP, duodrive.kicad_pcb, duodrive.kicad_sch]
2025-10-11 layout update
    [Screw Terminal Block 5mm 6-way.step, duodrive.kicad_pcb, duodrive.kicad_sch]
2025-10-13 finish and polishing
    [duodrive.kicad_pcb, duodrive.kicad_sch]
2025-11-02 PCB Upload
    [duodrive.kicad_pcb]
2025-11-09 layout and component changes
    [duodrive.kicad_pcb]

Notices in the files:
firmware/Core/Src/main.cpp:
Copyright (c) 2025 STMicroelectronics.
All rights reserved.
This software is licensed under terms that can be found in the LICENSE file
